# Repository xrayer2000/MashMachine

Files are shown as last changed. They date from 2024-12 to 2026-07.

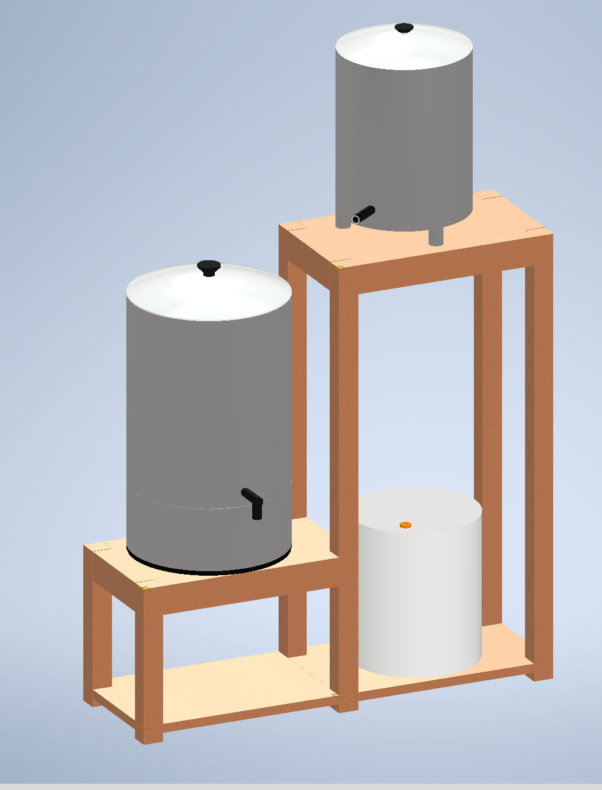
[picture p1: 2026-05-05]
InventorCad/BeerMakingShelf/5.png

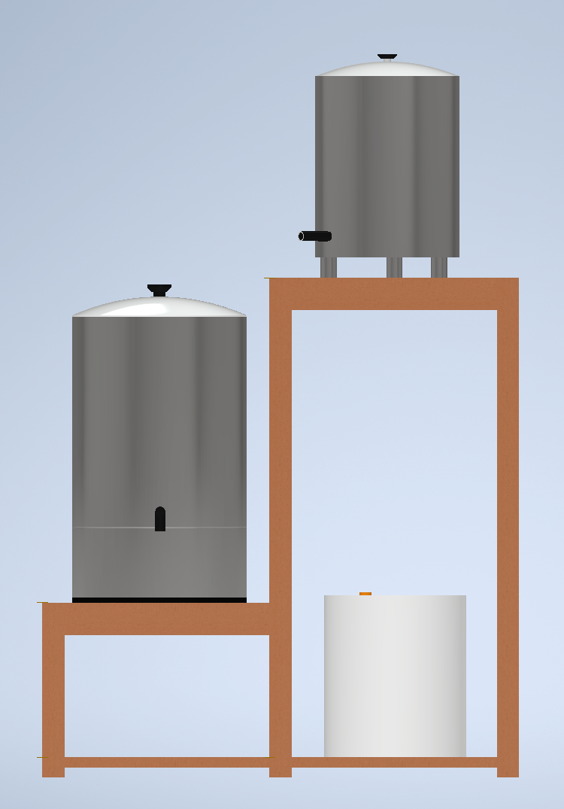
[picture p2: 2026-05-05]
InventorCad/BeerMakingShelf/6.png

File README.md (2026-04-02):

## Introduction - MashMachine
This project of mine has been a great journey for me to learn even more about my courses in the MPSYS (System Control and Mechatronics) program at Chalmers.

I have specifically used two courses in practice: SSY230 (System Identification) and SSY285 (Design of Linear Control Systems).

In the System Identification course, I used my mash tun to collect both estimation and validation data.

I used the System Identification Toolbox in MATLAB to derive state-space models for three different operating points: 50°C, 65°C, and 70°C.

EstimationData_65_75_85C

validationData_65_75_85C

ARMAX1200

All the system matrices were computed in MATLAB, and then implemented directly on the ESP32. The computational work was therefore performed offline, rather than on the microcontroller.

Once the state-space model was obtained, I used my other course, Design of Linear Control Systems, to design a controller based on this model.

I first implemented a state-feedback LQR controller, and later extended it to an LQG controller by adding a Kalman filter for state estimation.

This requires a state-space model, since LQG relies on an explicit representation of the system dynamics. In contrast to PID control, which operates only on the control error, LQG uses the model to estimate internal states and compute the control input.

With that said, the LQG controller was somewhat excessive for this application, since the system exhibits slow and stable dynamics. A PID controller would likely have been sufficient.

## Home Assistant Integration

The system is integrated with Home Assistant for monitoring and interaction.

A local Linux machine is used as a small server, running Home Assistant in a Docker container. The same setup also runs supporting services such as InfluxDB and Grafana.

Communication between the ESP32 and Home Assistant is handled using MQTT.

This setup allows:

Real-time monitoring of temperature, control signals, and system states  
Logging of data to InfluxDB for further analysis  
Visualization of system behaviour in Grafana  
Remote interaction through the Home Assistant interface  

The purpose of this integration is not only convenience, but also to enable data collection for system identification and validation, as well as to observe the controller performance over time.

## System Implementation

The starting point for this project was a very limited mash tun from Vevor, which only supported basic heating with its original controller.

The original system lacked proper control and exhibited temperature overshoot of around 2°C. To address this, the original controller was removed and replaced with a custom-built control system.

Several hardware modifications were made:

A circulation system was added using a pump  
Piping was installed to allow continuous wort circulation  
The original control electronics were replaced with an ESP32-based system  

The purpose of the circulation system is to improve temperature uniformity and make the system more suitable for control.

With the new controller, temperature regulation is significantly improved, with essentially no observable overshoot under normal operation.

In addition to the control system, several higher-level features were implemented:

-Hop timers 

-Mash programs 

-Automated process control logic 

-Home Assistant integration 

The Home Assistant integrationis is mainly for convenience, allowing me to monitor the mash process from anywhere.
The result is a system that not only performs better in terms of control, but also provides functionality expected from a more advanced brewing setup.

## Measurement System

The system initially used an NTC thermistor. This approach was abandoned due to calibration difficulty and unreliable results.

### NTC

The NTC sensor is strongly nonlinear and requires at least three reliable calibration points consisting of temperature and resistance.

In practice, this introduced several problems:

The calibration process was sensitive to noise  
Small resistance errors resulted in large temperature errors  
It was difficult to obtain consistent and accurate reference points  

This led to significant deviations between measured and actual temperature.

---

### PT100

The sensor was replaced with a PT100.

The main reasons were:

Near linear behaviour  
Simpler calibration, essentially gain and offset  
More stable and predictable measurements  

This change significantly improved both identification and state estimation.

---

## System Characteristics

The system exhibits slow dynamics and significant thermal inertia.

Measurements are affected by noise.

As a result, aggressive control is not appropriate. Stability and consistency are more important than fast response.

---

## Notes

The main difficulty in this project was not the controller design itself.

The critical parts were:

Obtaining reliable measurement data  
Constructing a model that reflects the real system  
Handling non-ideal behaviour in practice  

---

## Academic Context

This work is based on concepts from

System Identification  
Linear Control Design  

The objective has been to apply these methods to a real system rather than limiting the work to simulation.

---

## Result

A state-space model identified from experimental data  
An implemented LQG controller  
Stable temperature control on a physical system

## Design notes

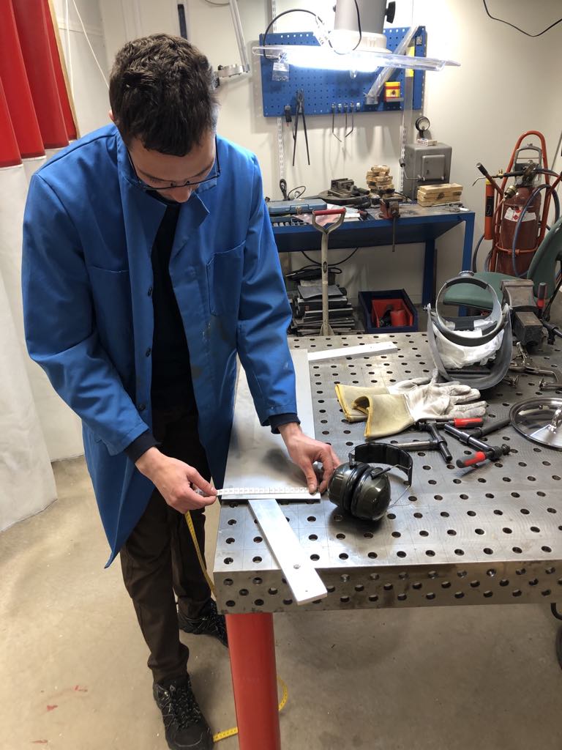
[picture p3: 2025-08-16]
PicturesAndMovies/Messenger_creation_4173f95c-cf8a-44c2-b453-e0ffb5a68564.jpeg

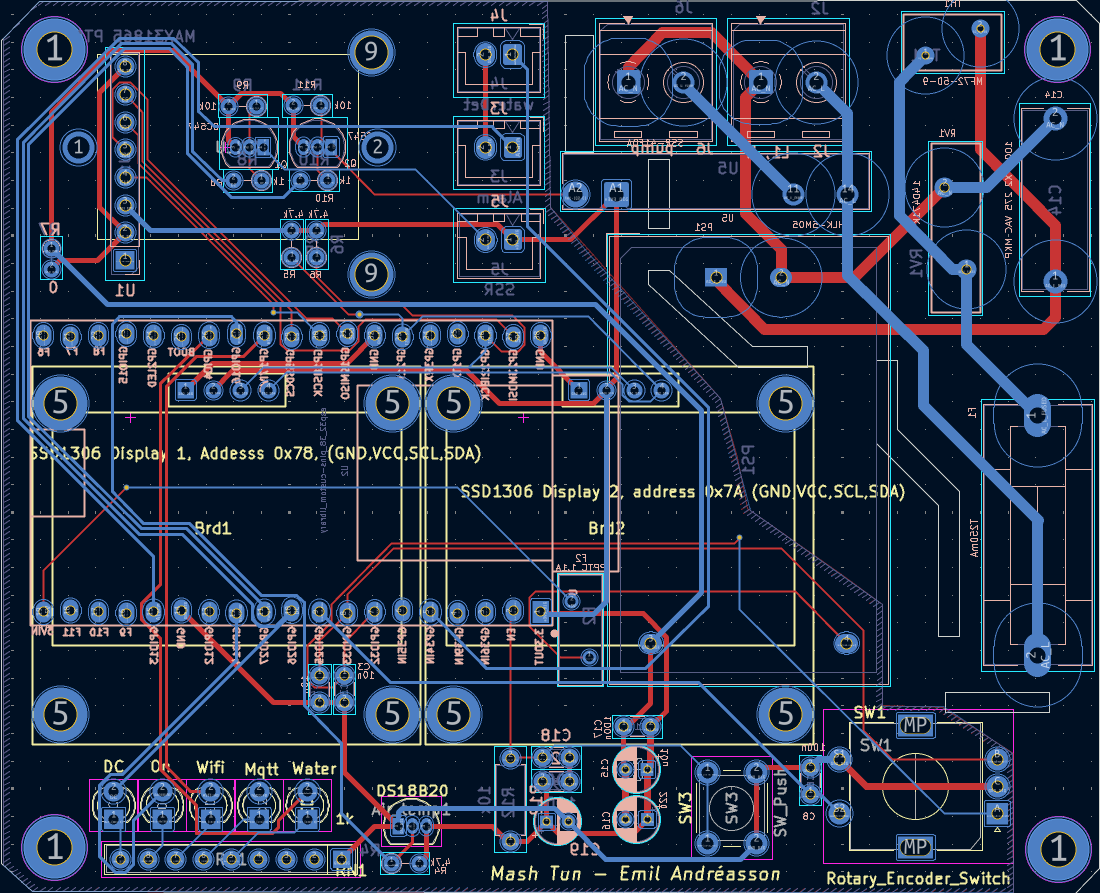
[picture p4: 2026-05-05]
InventorCad/Mash tank box V2.0/Lauter tank box/circuit board.png

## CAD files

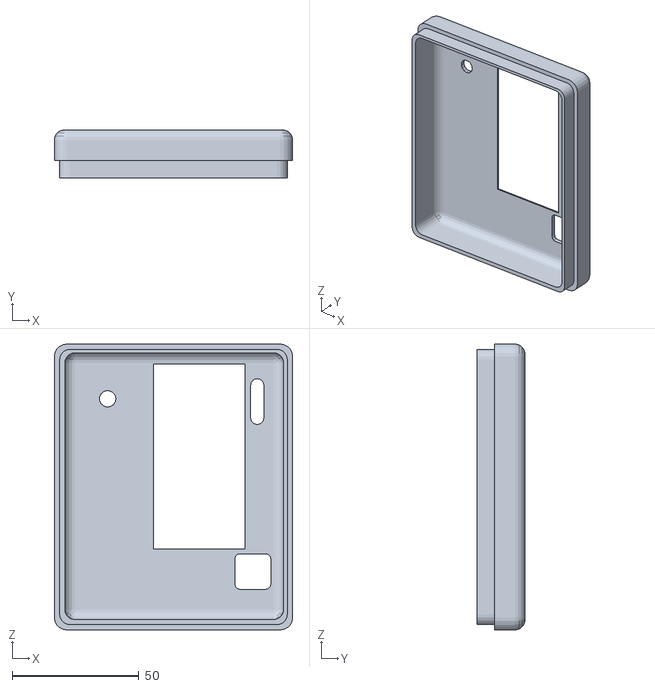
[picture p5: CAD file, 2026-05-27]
InventorCad/Lautering Tank box V2.0/lid_lautering_tank.stl
94.0 x 19.0 x 112.8

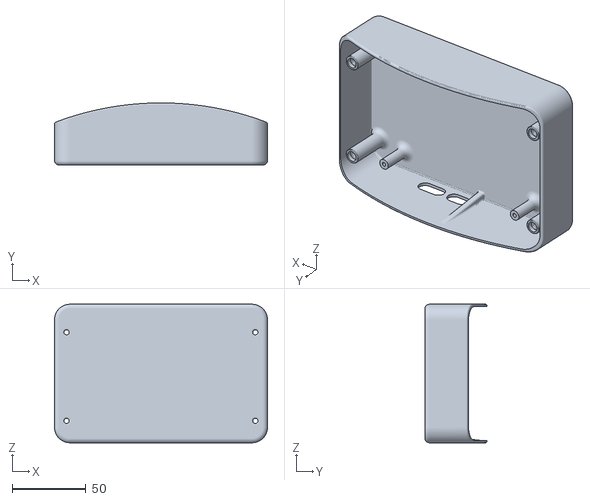
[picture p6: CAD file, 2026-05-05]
InventorCad/Mash tank box V2.0/Mash tank box/box.stl
143.9 x 42.0 x 93.7

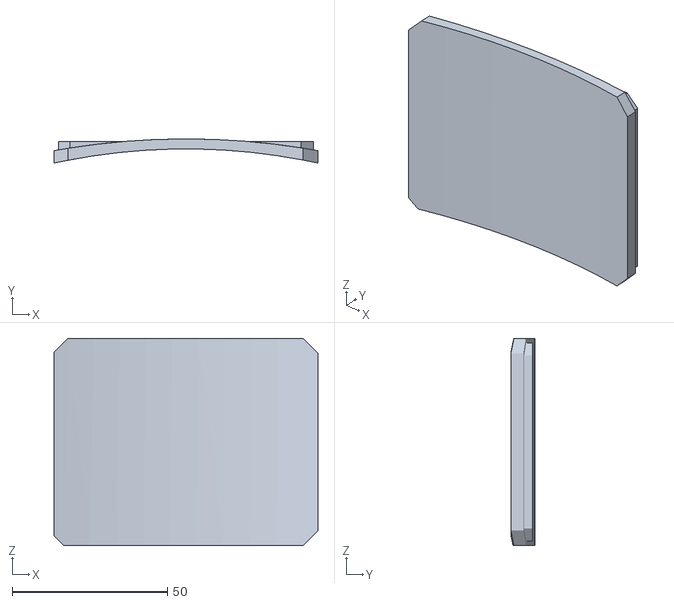
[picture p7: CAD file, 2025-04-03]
STL/Mash Tank Bottom.stl
85.1 x 7.80 x 66.8

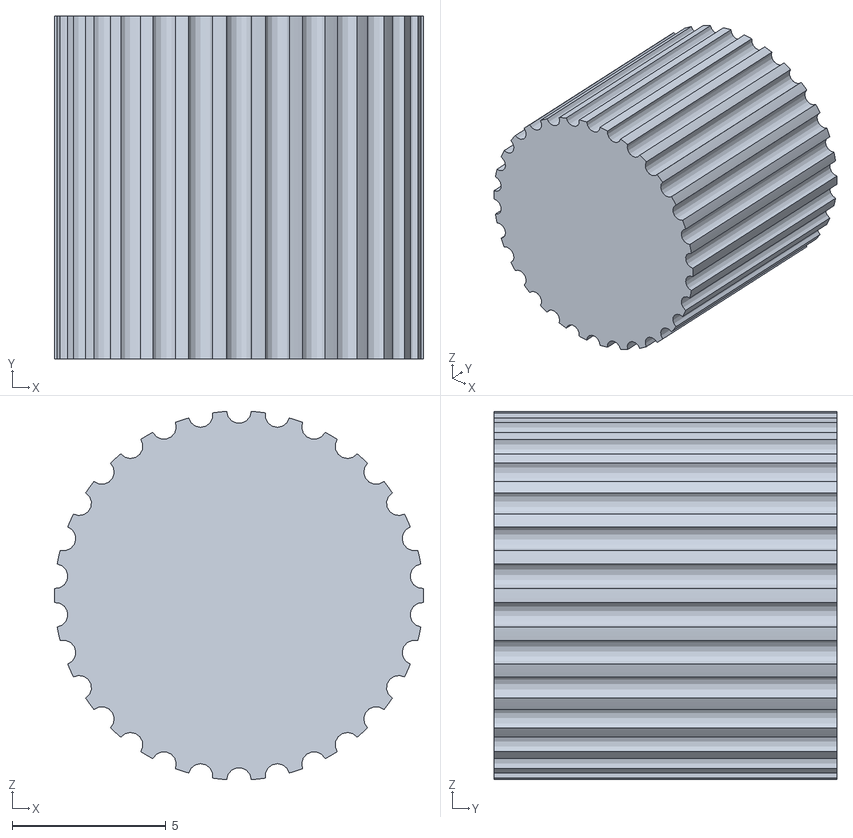
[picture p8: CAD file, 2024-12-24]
STL/Knob Rotory Encoder.stl
12.0 x 11.1 x 12.0

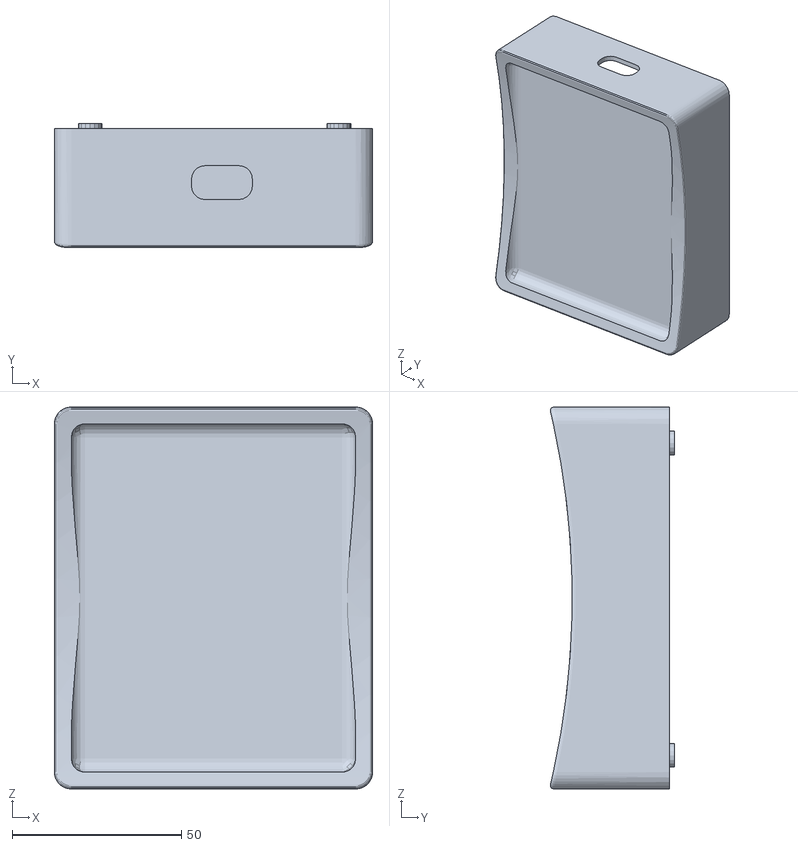
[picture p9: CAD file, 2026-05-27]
InventorCad/Lautering Tank box V2.0/lautering_tank_box.stl
94.0 x 36.7 x 112.8

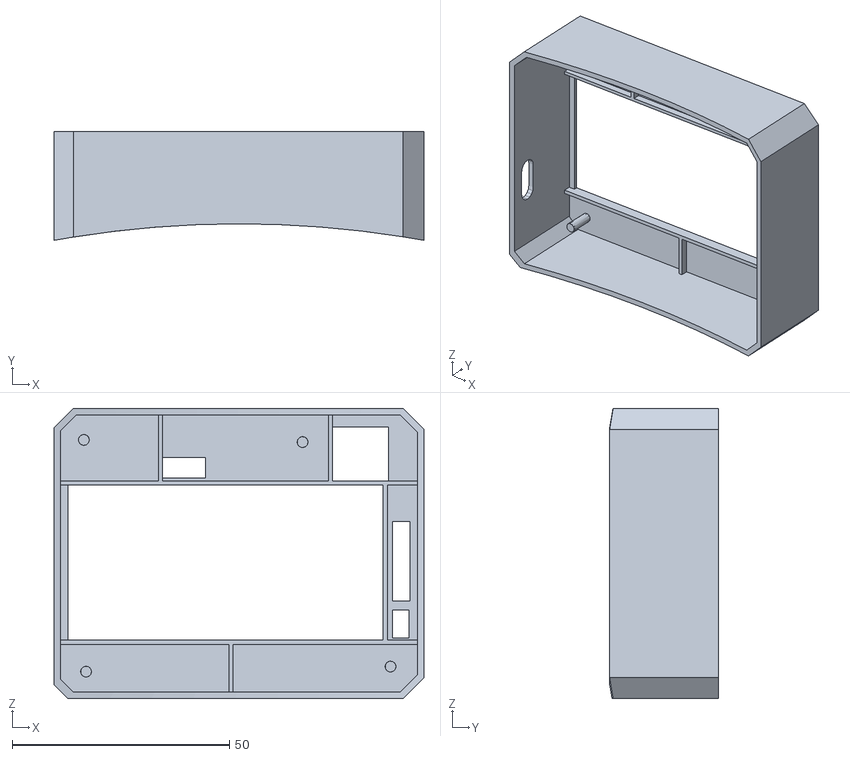
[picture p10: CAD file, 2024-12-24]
STL/Mash Tank Box.stl
85.1 x 25.0 x 66.8

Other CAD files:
InventorCad/Lautering Tank box V2.0/CE3V3SE_lid_lautering_tank.3mf
InventorCad/BeerMakingShelf/BeerMakingShelf.iam
InventorCad/BeerMakingShelf/FermentingTun.ipt
InventorCad/BeerMakingShelf/LauteringTun.ipt
InventorCad/BeerMakingShelf/MashMaschine V2.0 modell.ipt
InventorCad/BeerMakingShelf/Mäskmaskin.ipt
InventorCad/BeerMakingShelf/OldVersions/BeerMakingShelf.0038.iam
InventorCad/BeerMakingShelf/OldVersions/FermentingTun.0002.ipt
InventorCad/BeerMakingShelf/OldVersions/LauteringTun.0008.ipt
InventorCad/BeerMakingShelf/OldVersions/MashMaschine V2.0 modell.0006.ipt
InventorCad/BeerMakingShelf/OldVersions/Shelf.0003.ipt
InventorCad/BeerMakingShelf/OldVersions/selfBeamShort.0001.ipt
InventorCad/BeerMakingShelf/OldVersions/shelfBeam.0008.ipt
InventorCad/BeerMakingShelf/OldVersions/shelfBeamSide.0002.ipt
InventorCad/BeerMakingShelf/Shelf.ipt
InventorCad/BeerMakingShelf/selfBeamLong.ipt
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

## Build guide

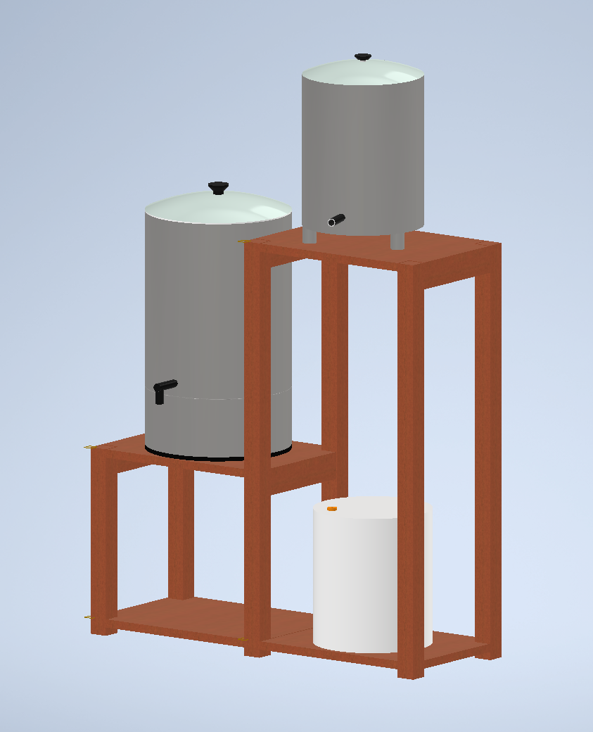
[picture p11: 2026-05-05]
InventorCad/BeerMakingShelf/3.png

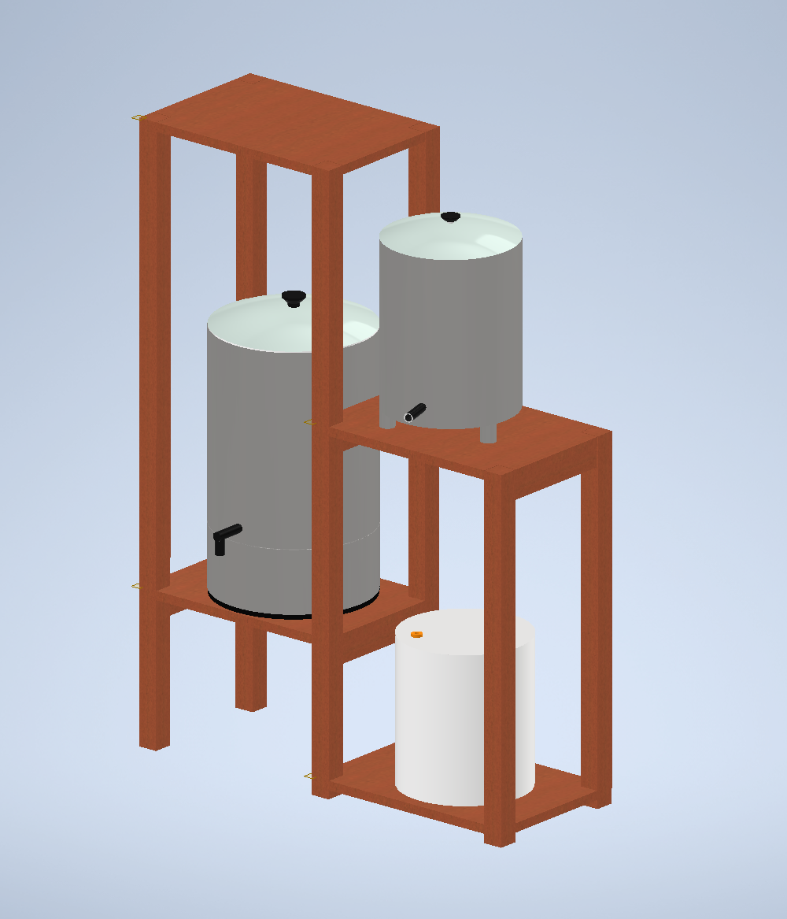
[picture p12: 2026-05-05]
InventorCad/BeerMakingShelf/2.png

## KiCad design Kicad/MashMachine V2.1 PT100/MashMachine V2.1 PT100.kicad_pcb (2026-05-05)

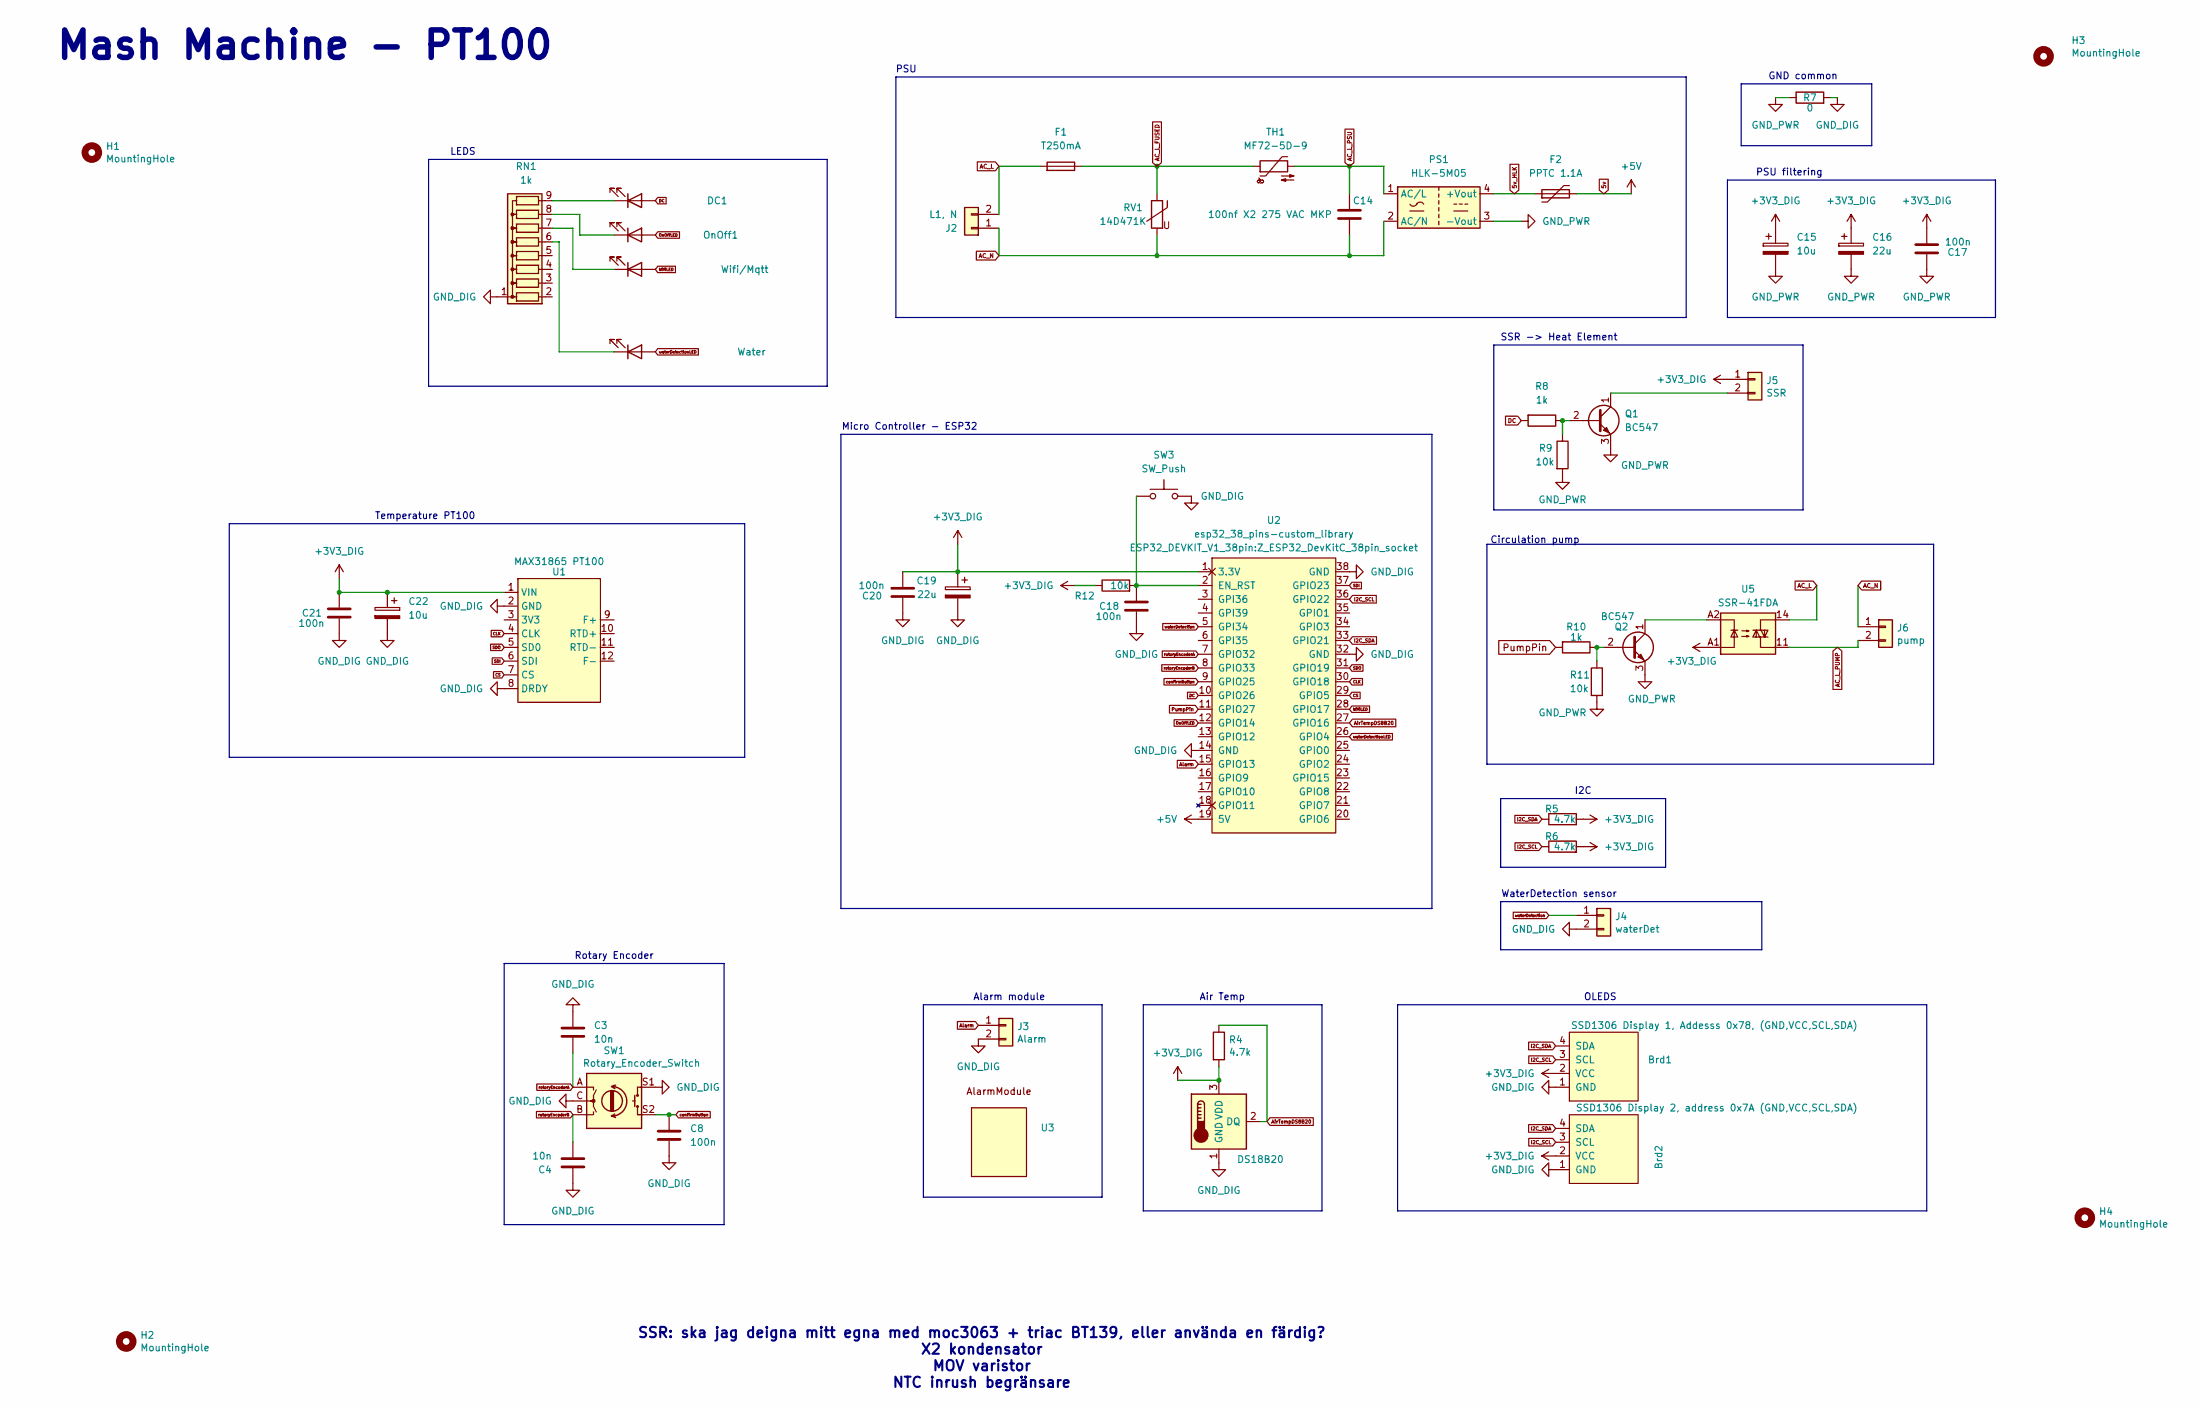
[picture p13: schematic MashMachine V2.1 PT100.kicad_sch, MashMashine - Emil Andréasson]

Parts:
Air_temp1: DS18B20; TO-92L_Inline
Brd1: SSD1306 Display 1, Addesss 0x78, (GND,VCC,SCL,SDA); ssd1306_1.3''
Brd2: SSD1306 Display 2, address 0x7A (GND,VCC,SCL,SDA); ssd1306_1.3''
C3, C4: 10n; C_Disc_D3.0mm_W1.6mm_P2.50mm
C8, C17, C18, C20, C21: 100n; C_Disc_D3.0mm_W1.6mm_P2.50mm
C14: 100nf X2 275 VAC MKP; C_Rect_L16.5mm_W6.0mm_P15.00mm_MKT
C15, C22: 10u; CP_Radial_D4.0mm_P2.00mm
C16, C19: 22u; CP_Radial_D4.0mm_P2.00mm
DC1: DC; LED_D3.0mm
F1: T250mA; Fuseholder5x20_horiz_SemiClosed_Casing10x25mm
F2: PPTC 1.1A; Fuse_BelFuse_0ZRE0016FF_L9.9mm_W3.8mm
H1, H2, H3, H4: MountingHole; MountingHole_3.2mm_M3_DIN965_Pad
J2: L1, N; TerminalBlock_RND_205-00287_1x02_P5.08mm_Horizontal
J3: Alarm; JST_XH_B2B-XH-A_1x02_P2.50mm_Vertical
J4: waterDet; JST_XH_B2B-XH-A_1x02_P2.50mm_Vertical
J5: SSR; JST_XH_B2B-XH-A_1x02_P2.50mm_Vertical
J6: pump; TerminalBlock_RND_205-00287_1x02_P5.08mm_Horizontal
LED1: Wifi/Mqtt; LED_D3.0mm
LED3: Water; LED_D3.0mm
OnOff1: On; LED_D3.0mm
PS1: HLK-5M05; Converter_ACDC_Hi-Link_HLK-5Mxx
Q1, Q2: BC547; TO-92_Inline
R4, R5, R6: 4.7k; R_Axial_DIN0204_L3.6mm_D1.6mm_P2.54mm_Vertical
R7: 0; R_Axial_DIN0204_L3.6mm_D1.6mm_P1.90mm_Vertical
R8, R10: 1k; R_Axial_DIN0204_L3.6mm_D1.6mm_P2.54mm_Vertical
R9, R11: 10k; R_Axial_DIN0204_L3.6mm_D1.6mm_P2.54mm_Vertical
R12: 10k; R_Axial_DIN0207_L6.3mm_D2.5mm_P7.62mm_Horizontal
RN1: 1k; R_Array_SIP9
RV1: 14D471K; RV_Disc_D15.5mm_W4.5mm_P7.5mm
SW1: Rotary_Encoder_Switch; RotaryEncoder_Alps_EC11E-Switch_Vertical_H20mm
SW3: SW_Push; SW_PUSH_6mm
TH1: MF72-5D-9; RV_Disc_D9mm_W5.2mm_P5mm
U1: MAX31865 PT100; PinSocket_1x08_P2.54mm_Vertical
U2: esp32_38_pins-custom_library; Z_ESP32_DevKitC_38pin_socket
U3: AlarmModule
U5: SSR-41FDA; Finder_34.81

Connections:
5v: F2.2, U2.19 (5V)
5v_HLK: F2.1, PS1.4 (+Vout)
+3V3_DIG: Air_temp1.3 (VDD), Brd1.2 (VCC), Brd2.2 (VCC), C15.1, C16.1, C17.2, C19.1, C20.2, C21.2, C22.1, J5.1, R4.2, R5.2, R6.2, R12.1, U1.1 (VIN), U2.1 (3.3V), U5.A1
AC_L: F1.2, J2.2, U5.14
AC_L_FUSED: F1.1, RV1.1, TH1.1
AC_L_PSU: C14.1, PS1.1 (AC/L), TH1.2
AC_L_PUMP: J6.2, U5.11
AC_N: C14.2, J2.1, J6.1, PS1.2 (AC/N), RV1.2
AirTempDS8B20: Air_temp1.2 (DQ), R4.1, U2.27 (GPIO16)
Alarm: J3.1, U2.15 (GPIO13)
CLK: U1.4 (CLK), U2.30 (GPIO18)
CS: U1.7 (CS), U2.29 (GPIO5)
DC: DC1.2 (A), R8.2, U2.10 (GPIO26)
GND_DIG: Air_temp1.1 (GND), Brd1.1 (GND), Brd2.1 (GND), C3.2, C4.2, C8.2, C18.1, C19.2, C20.1, C21.1, C22.2, J3.2, J4.2, R7.2, RN1.1 (common), SW1.C, SW1.S1, SW3.2, U1.2 (GND), U1.8 (DRDY), U2.14 (GND), U2.32 (GND), U2.38 (GND)
GND_PWR: C15.2, C16.2, C17.1, PS1.3 (-Vout), Q1.3 (E), Q2.3 (E), R7.1, R9.2, R11.2
I2C_SCL: Brd1.3 (SCL), Brd2.3 (SCL), R6.1, U2.36 (GPIO22)
I2C_SDA: Brd1.4 (SDA), Brd2.4 (SDA), R5.1, U2.33 (GPIO21)
unnamed: DC1.1 (K), RN1.9 (R8)
unnamed: J5.2, Q1.1 (C)
unnamed: LED1.1 (K), RN1.7 (R6)
unnamed: LED3.1 (K), RN1.6 (R5)
unnamed: OnOff1.1 (K), RN1.8 (R7)
unnamed: Q1.2 (B), R8.1, R9.1
unnamed: Q2.2 (B), R10.1, R11.1
unnamed: Q2.1 (C), U5.A2
unnamed: C18.2, R12.2, SW3.1, U2.2 (EN_RST)
OnOffLED: OnOff1.2 (A), U2.12 (GPIO14)
PumpPin: R10.2, U2.11 (GPIO27)
SDI: U1.6 (SDI), U2.37 (GPIO23)
SDO: U1.5 (SD0), U2.31 (GPIO19)
WifiLED: LED1.2 (A), U2.28 (GPIO17)
confirmButton: C8.1, SW1.S2, U2.9 (GPIO25)
rotoryEncoderA: C3.1, SW1.A, U2.7 (GPIO32)
rotoryEncoderB: C4.1, SW1.B, U2.8 (GPIO33)
waterDetection: J4.1, U2.5 (GPI34)
waterDetectionLED: LED3.2 (A), U2.26 (GPIO4)

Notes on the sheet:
LEDS
GND common
Rotary Encoder
OLEDS
Micro Controller - ESP32
Circulation pump
SSR -> Heat Element
Alarm module
Air Temp
Mash Machine - PT100
PSU filtering
SSR: ska jag deigna mitt egna med moc3063 + triac BT139, eller använda en färdig? X2 kondensator MOV varistor NTC inrush begränsare
PSU
WaterDetection sensor
I2C
Temperature PT100

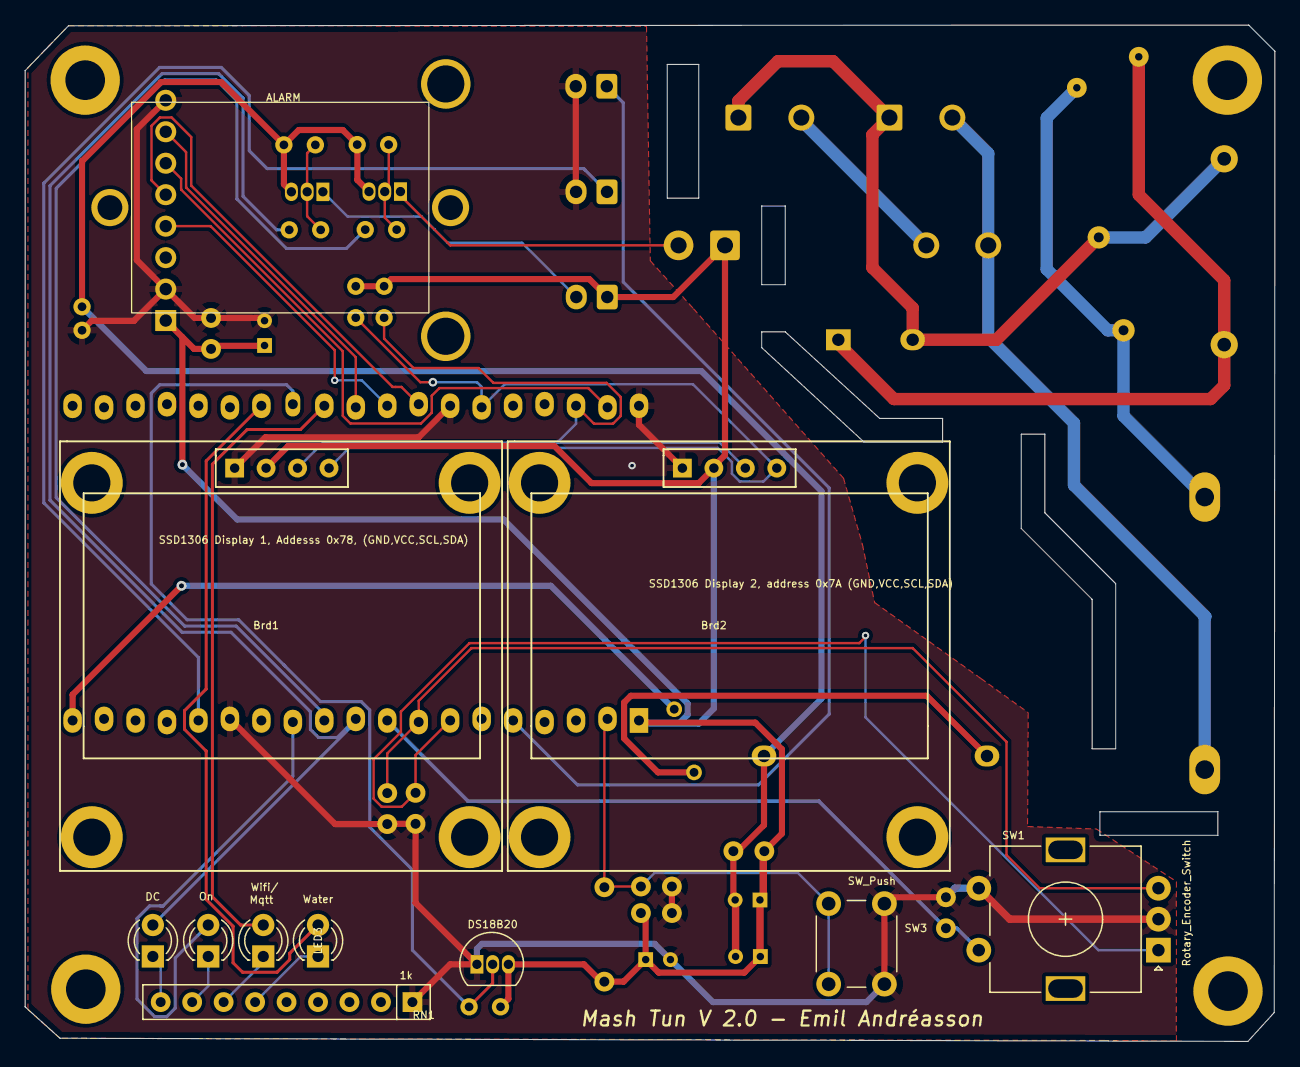
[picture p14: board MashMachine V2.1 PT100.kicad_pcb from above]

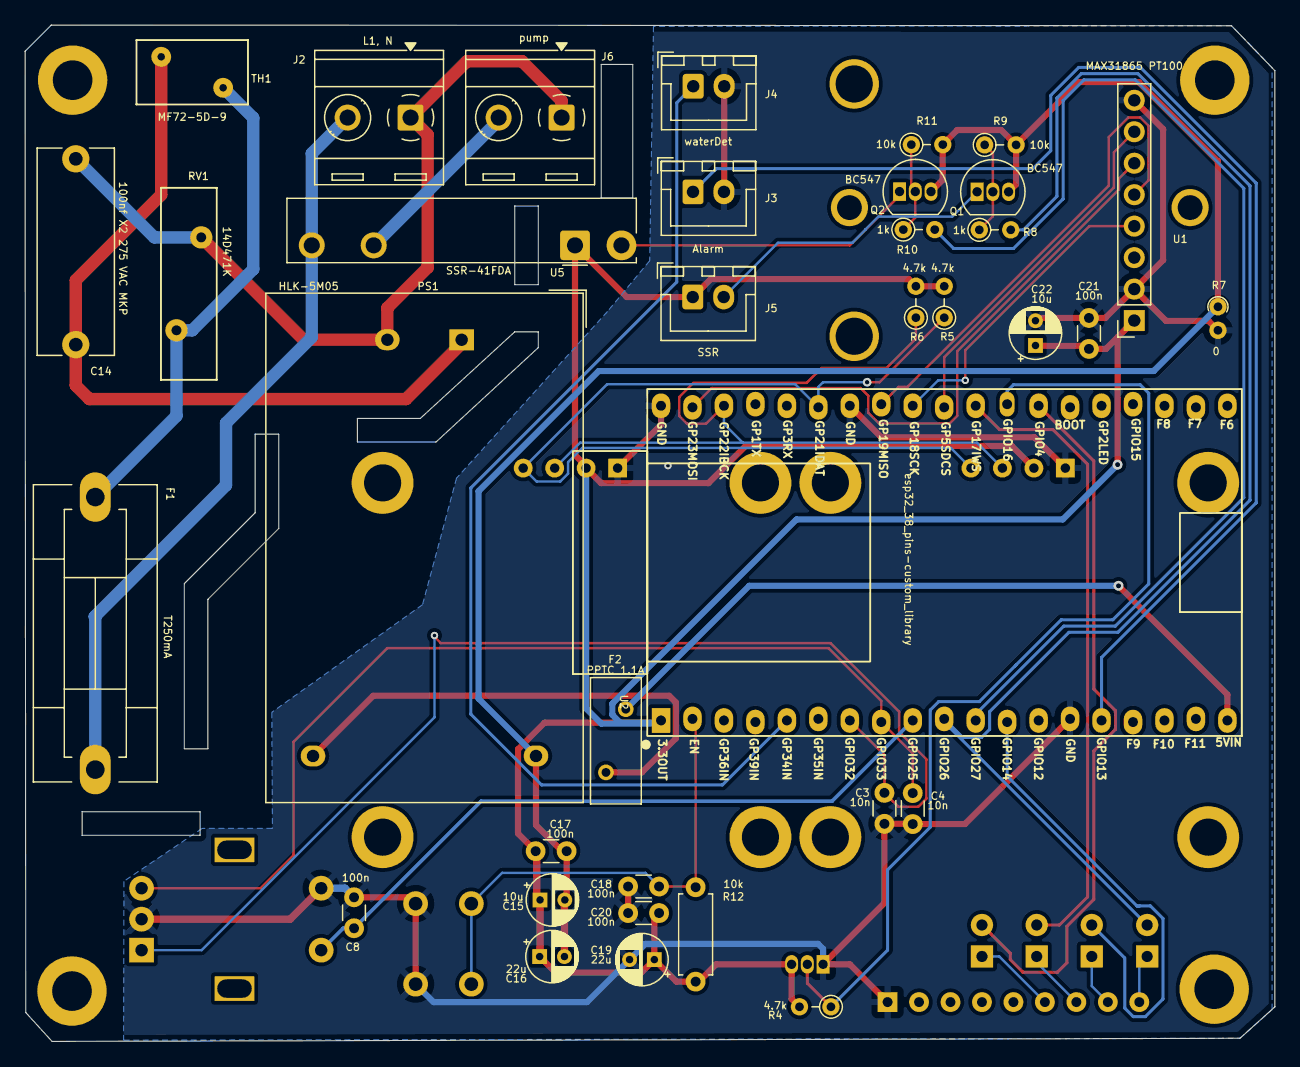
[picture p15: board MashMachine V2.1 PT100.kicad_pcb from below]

Board: 2 copper layers, 100.9 x 82.0 mm, 51 parts (36 on the bottom side), 36 nets.

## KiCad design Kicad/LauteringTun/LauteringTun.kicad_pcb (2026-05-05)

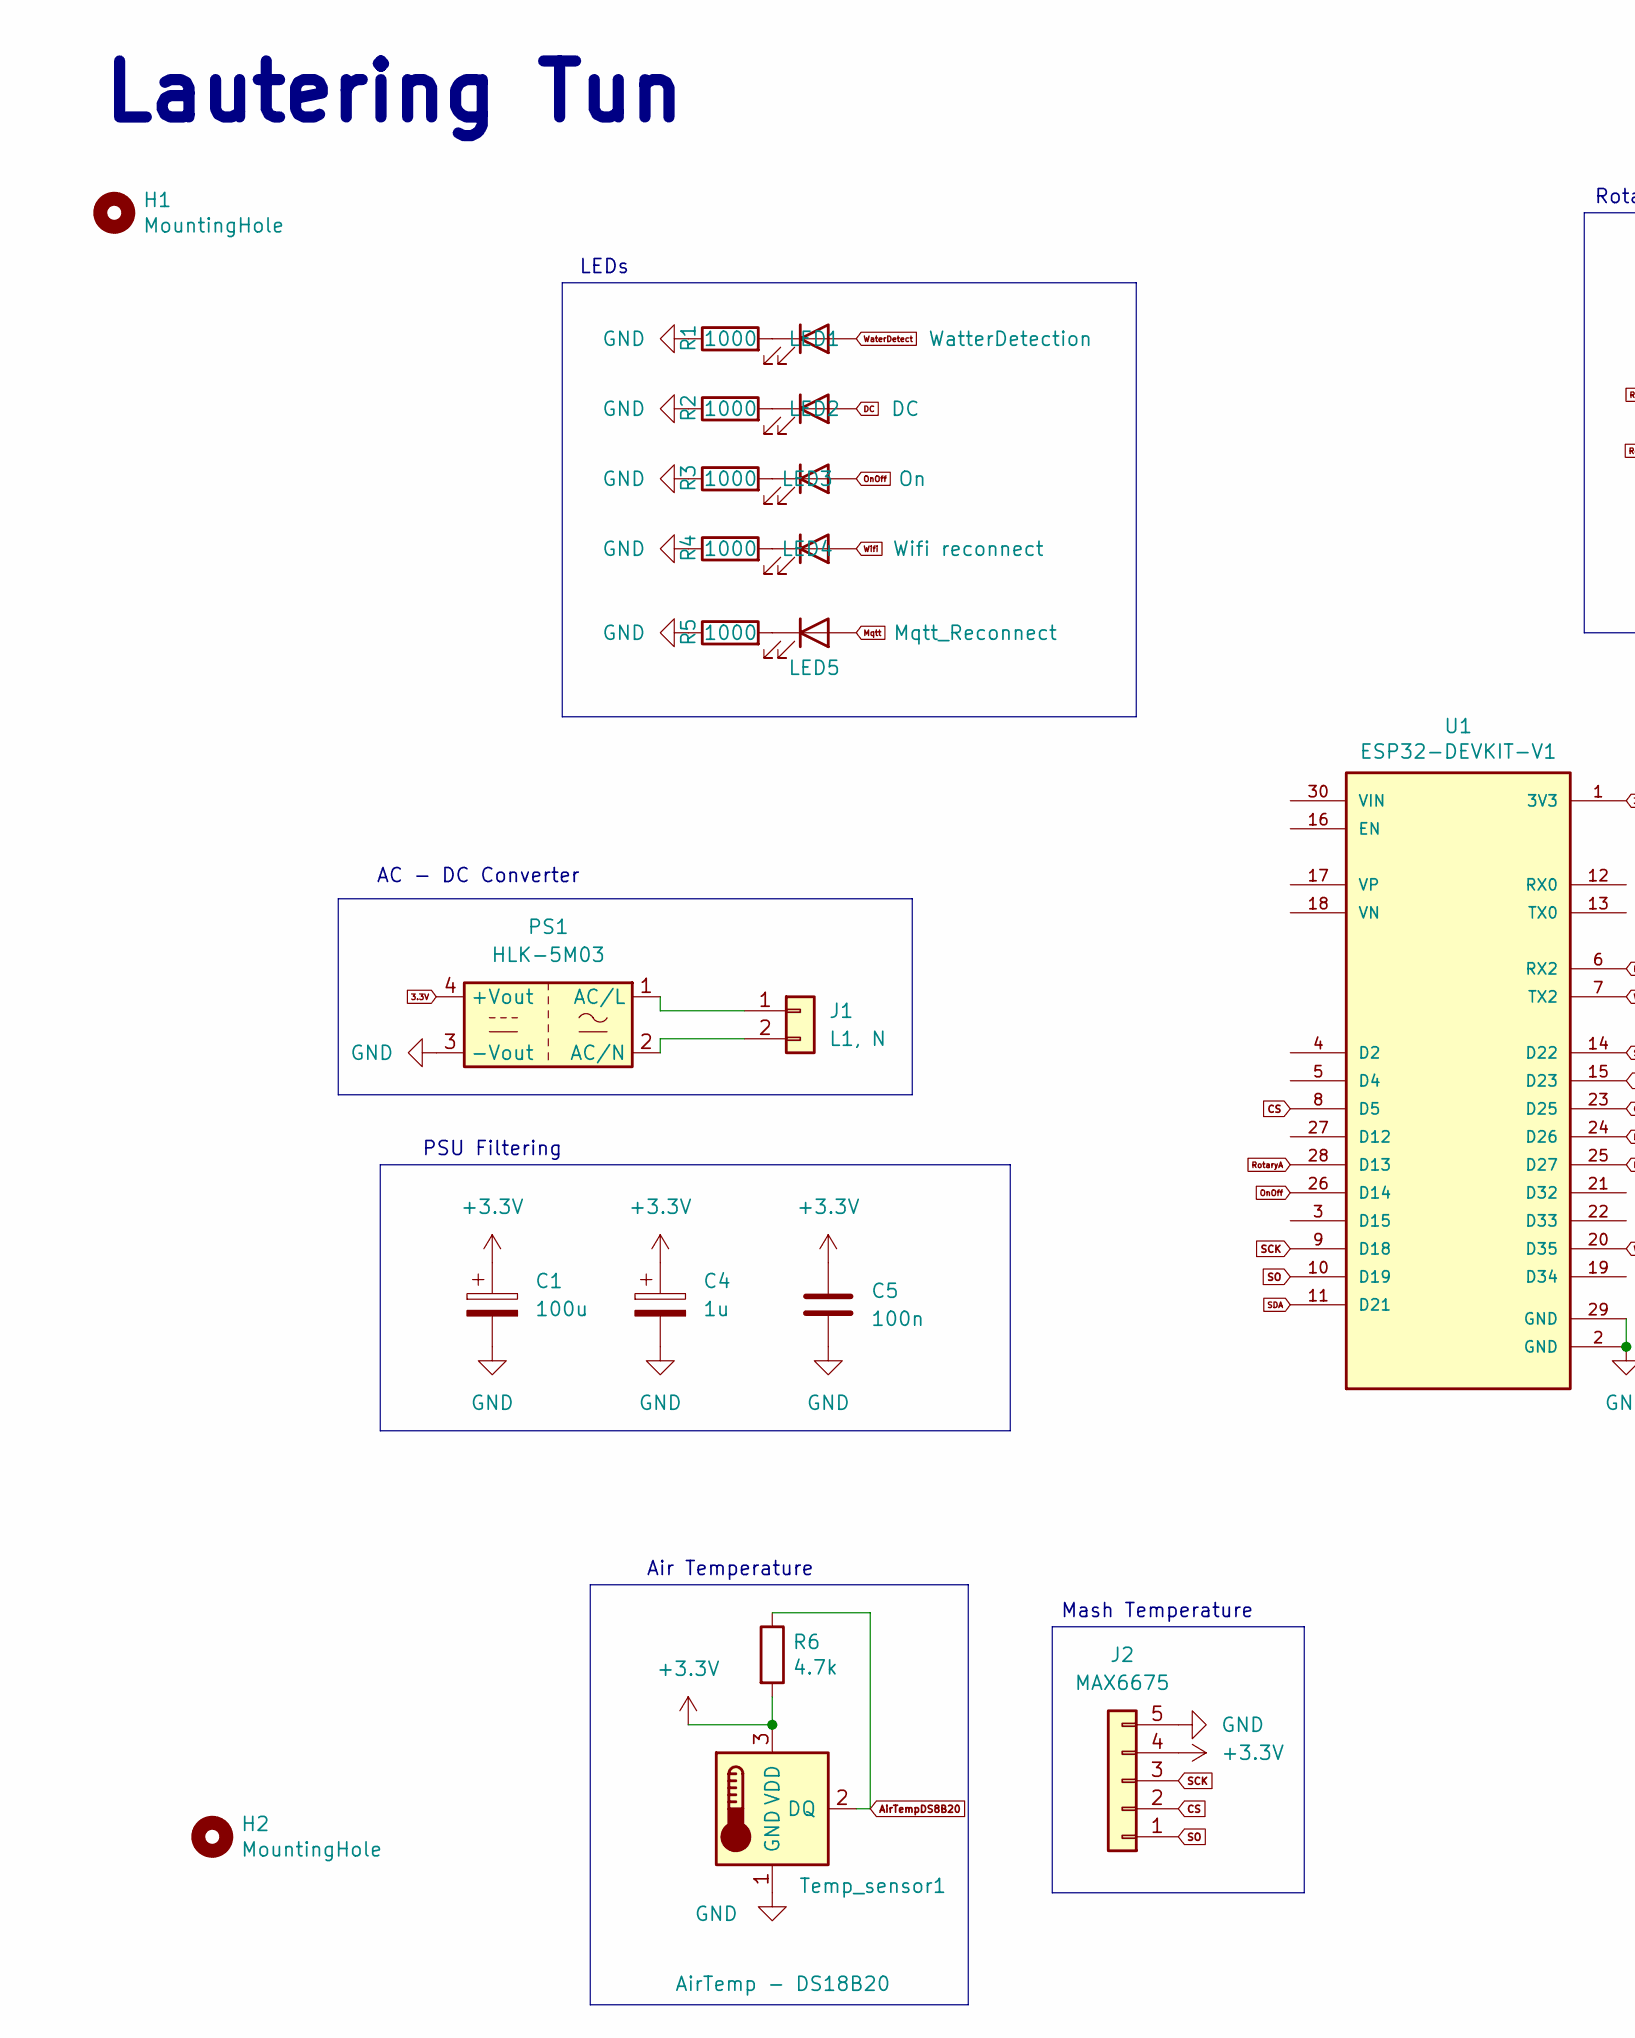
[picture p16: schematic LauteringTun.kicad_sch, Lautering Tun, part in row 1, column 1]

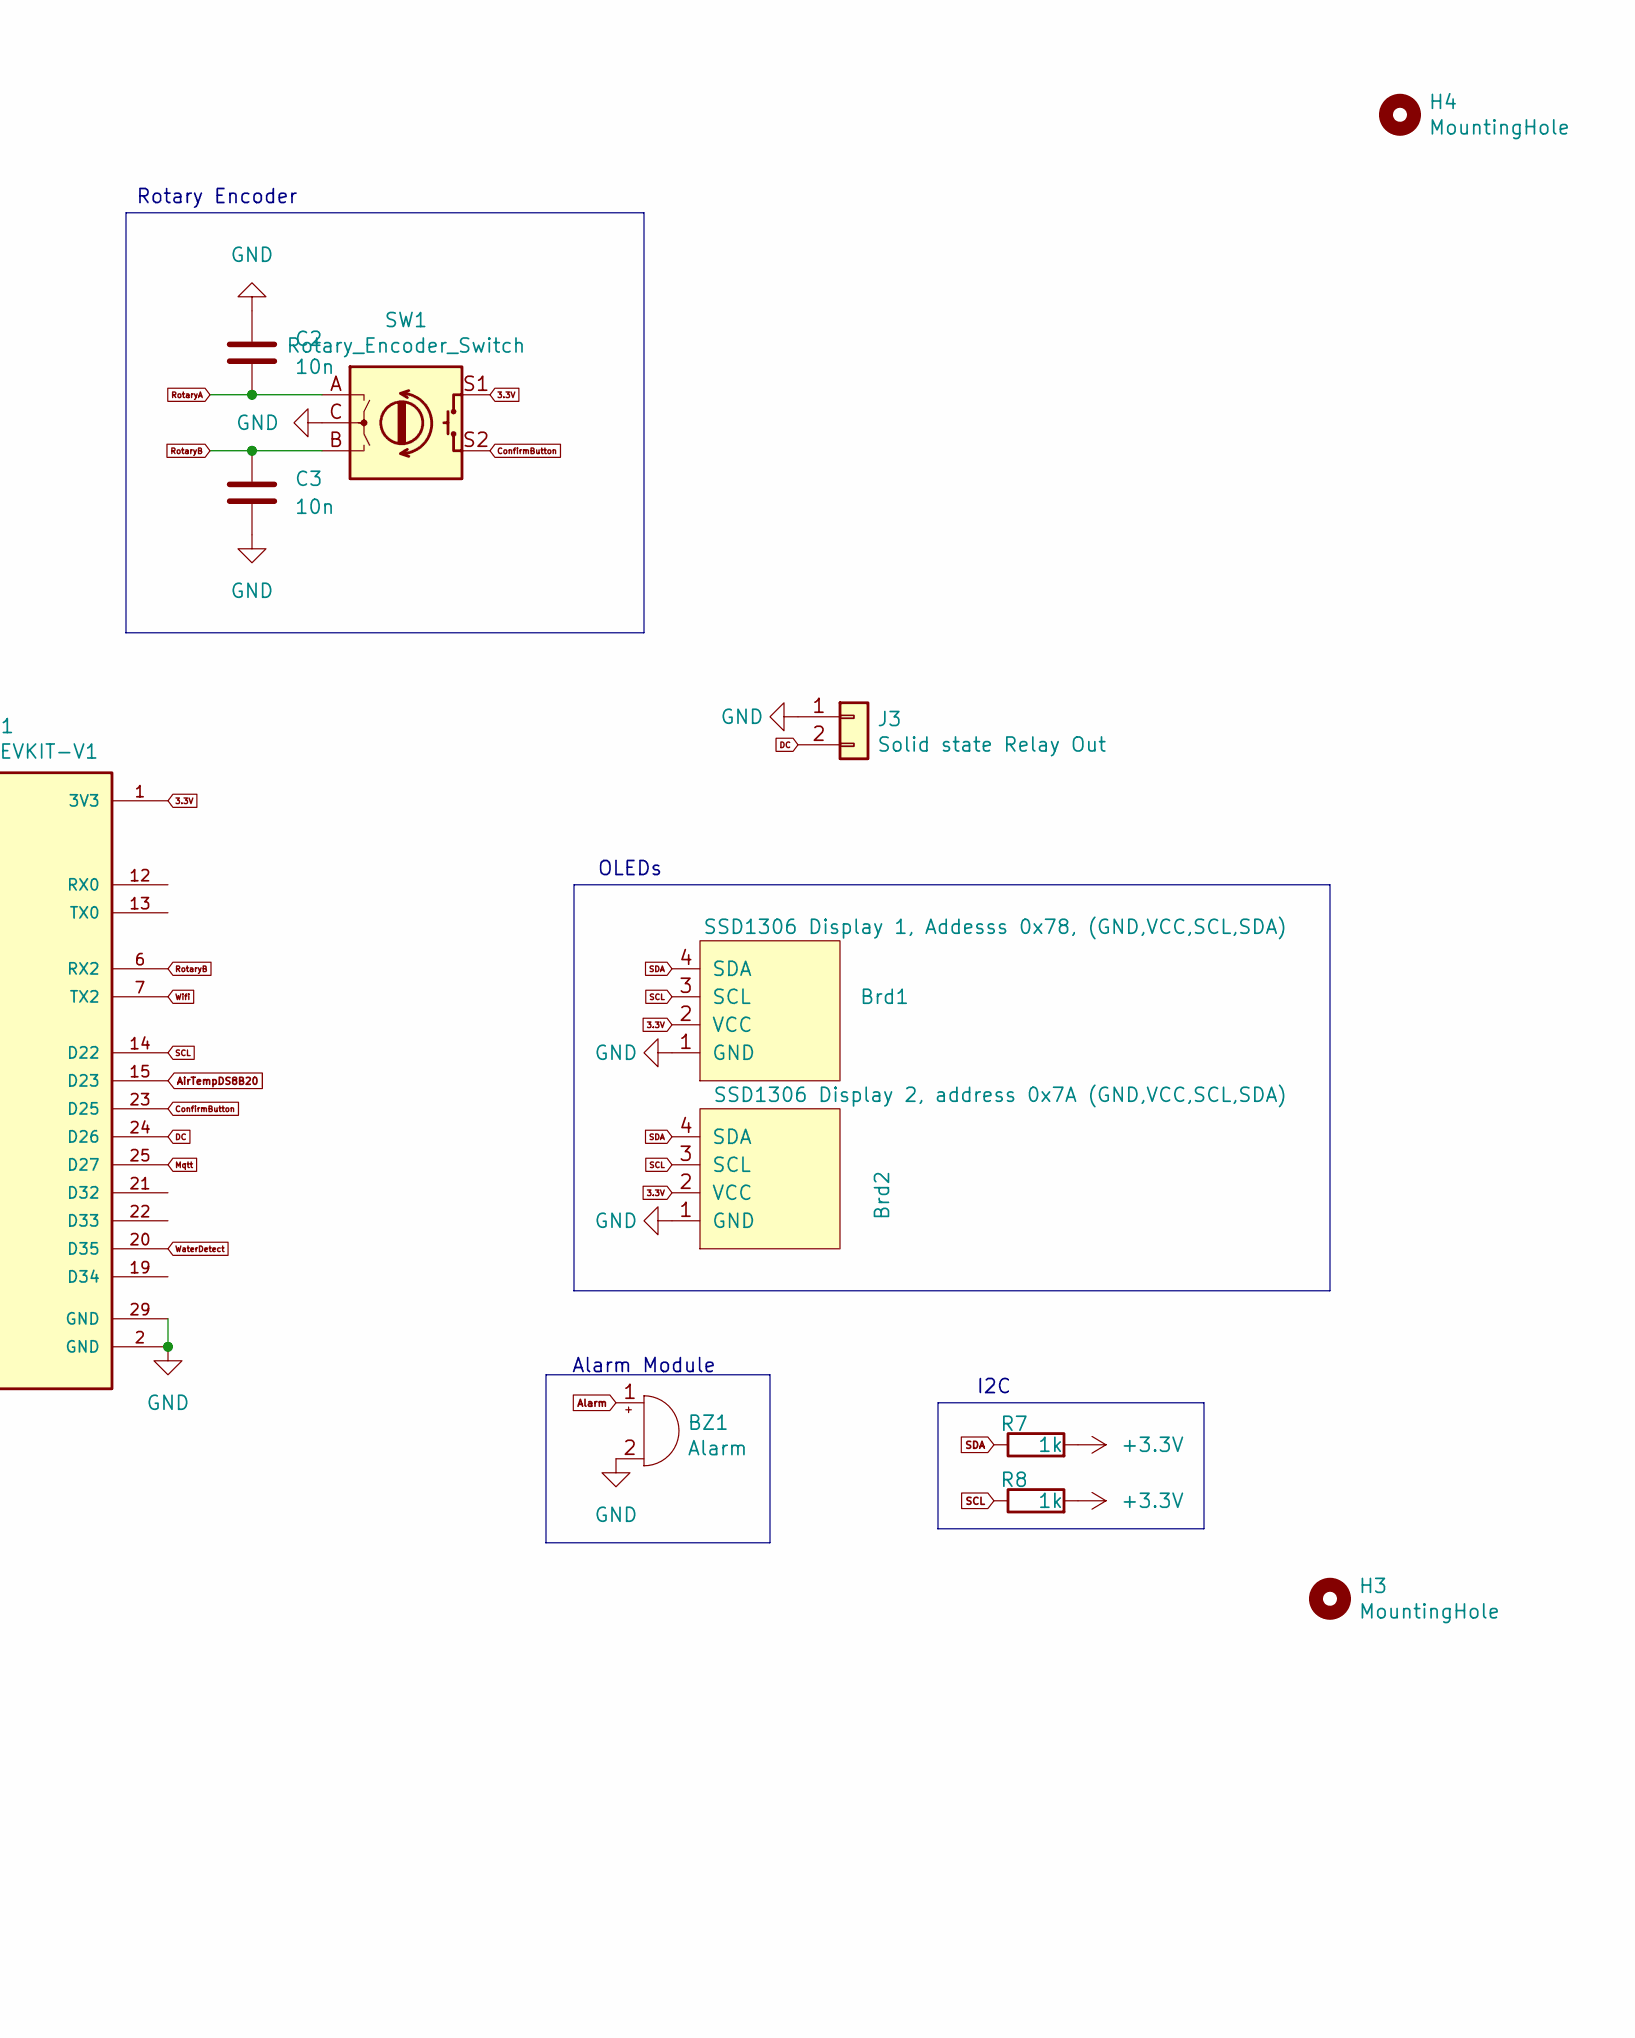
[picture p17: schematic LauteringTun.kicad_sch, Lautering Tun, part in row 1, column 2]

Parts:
BZ1: Alarm; Buzzer_12x9.5RM7.6
Brd1: SSD1306 Display 1, Addesss 0x78, (GND,VCC,SCL,SDA); ssd1306_1.3''
Brd2: SSD1306 Display 2, address 0x7A (GND,VCC,SCL,SDA); ssd1306_1.3''
C1: 100u; CP_Radial_D4.0mm_P2.00mm
C2, C3: 10n; C_Disc_D3.0mm_W1.6mm_P2.50mm
C4: 1u; CP_Radial_D4.0mm_P2.00mm
C5: 100n; C_Disc_D3.0mm_W1.6mm_P2.50mm
H1, H2, H3, H4: MountingHole; MountingHole_3.2mm_M3_DIN965_Pad
J1: L1, N; TerminalBlock_Phoenix_MKDS-1,5-2_1x02_P5.00mm_Horizontal
J2: MAX6675
J3: Solid state Relay Out; JST_XH_B2B-XH-A_1x02_P2.50mm_Vertical
LED1: WatterDetection; LED_D3.0mm
LED2: DC; LED_D3.0mm
LED3: On; LED_D3.0mm
LED4: Wifi reconnect; LED_D3.0mm
LED5: Mqtt_Reconnect; LED_D3.0mm
PS1: HLK-5M03; Converter_ACDC_Hi-Link_HLK-5Mxx
R1, R2, R3, R4, R5: 1000; R_Axial_DIN0207_L6.3mm_D2.5mm_P7.62mm_Horizontal
R6: 4.7k; R_Axial_DIN0207_L6.3mm_D2.5mm_P10.16mm_Horizontal
R7, R8: 1k; R_Axial_DIN0207_L6.3mm_D2.5mm_P7.62mm_Horizontal
SW1: Rotary_Encoder_Switch; RotaryEncoder_Alps_EC11E-Switch_Vertical_H20mm
Temp_sensor1: AirTemp - DS18B20; TO-92L_Inline
U1: ESP32-DEVKIT-V1; ESP32_DEVKIT_V1; PARTREV N/A

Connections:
3.3V: Brd1.2 (VCC), Brd2.2 (VCC), PS1.4 (+Vout), SW1.S1, U1.1 (3V3)
+3.3V: C1.1, C4.1, C5.2, J2.4, R6.2, R7.2, R8.2, Temp_sensor1.3 (VDD)
AirTempDS8B20: R6.1, Temp_sensor1.2 (DQ), U1.15 (D23)
Alarm: BZ1.1 (-)
CS: J2.2, U1.8 (D5)
ConfirmButton: SW1.S2, U1.23 (D25)
DC: J3.2, LED2.2 (A), U1.24 (D26)
GND: BZ1.2 (+), Brd1.1 (GND), Brd2.1 (GND), C1.2, C2.2, C3.1, C4.2, C5.1, J2.5, J3.1, PS1.3 (-Vout), R1.1, R2.1, R3.1, R4.1, R5.1, SW1.C, Temp_sensor1.1 (GND), U1.2 (GND), U1.29 (GND)
Mqtt: LED5.2 (A), U1.25 (D27)
unnamed: J1.1, PS1.1 (AC/L)
unnamed: J1.2, PS1.2 (AC/N)
unnamed: LED1.1 (K), R1.2
unnamed: LED2.1 (K), R2.2
unnamed: LED3.1 (K), R3.2
unnamed: LED4.1 (K), R4.2
unnamed: LED5.1 (K), R5.2
OnOff: LED3.2 (A), U1.26 (D14)
RotaryA: C2.1, SW1.A, U1.28 (D13)
RotaryB: C3.2, SW1.B, U1.6 (RX2)
SCK: J2.3, U1.9 (D18)
SCL: Brd1.3 (SCL), Brd2.3 (SCL), R8.1, U1.14 (D22)
SDA: Brd1.4 (SDA), Brd2.4 (SDA), R7.1, U1.11 (D21)
SO: J2.1, U1.10 (D19)
WaterDetect: LED1.2 (A), U1.20 (D35)
Wifi: LED4.2 (A), U1.7 (TX2)

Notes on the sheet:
I2C
Alarm Module
AC - DC Converter
Air Temperature
Lautering Tun
OLEDs
Mash Temperature
LEDs
PSU Filtering
Rotary Encoder

Board: 2 copper layers, 32 parts (2 on the bottom side), 24 nets, no tracks yet.

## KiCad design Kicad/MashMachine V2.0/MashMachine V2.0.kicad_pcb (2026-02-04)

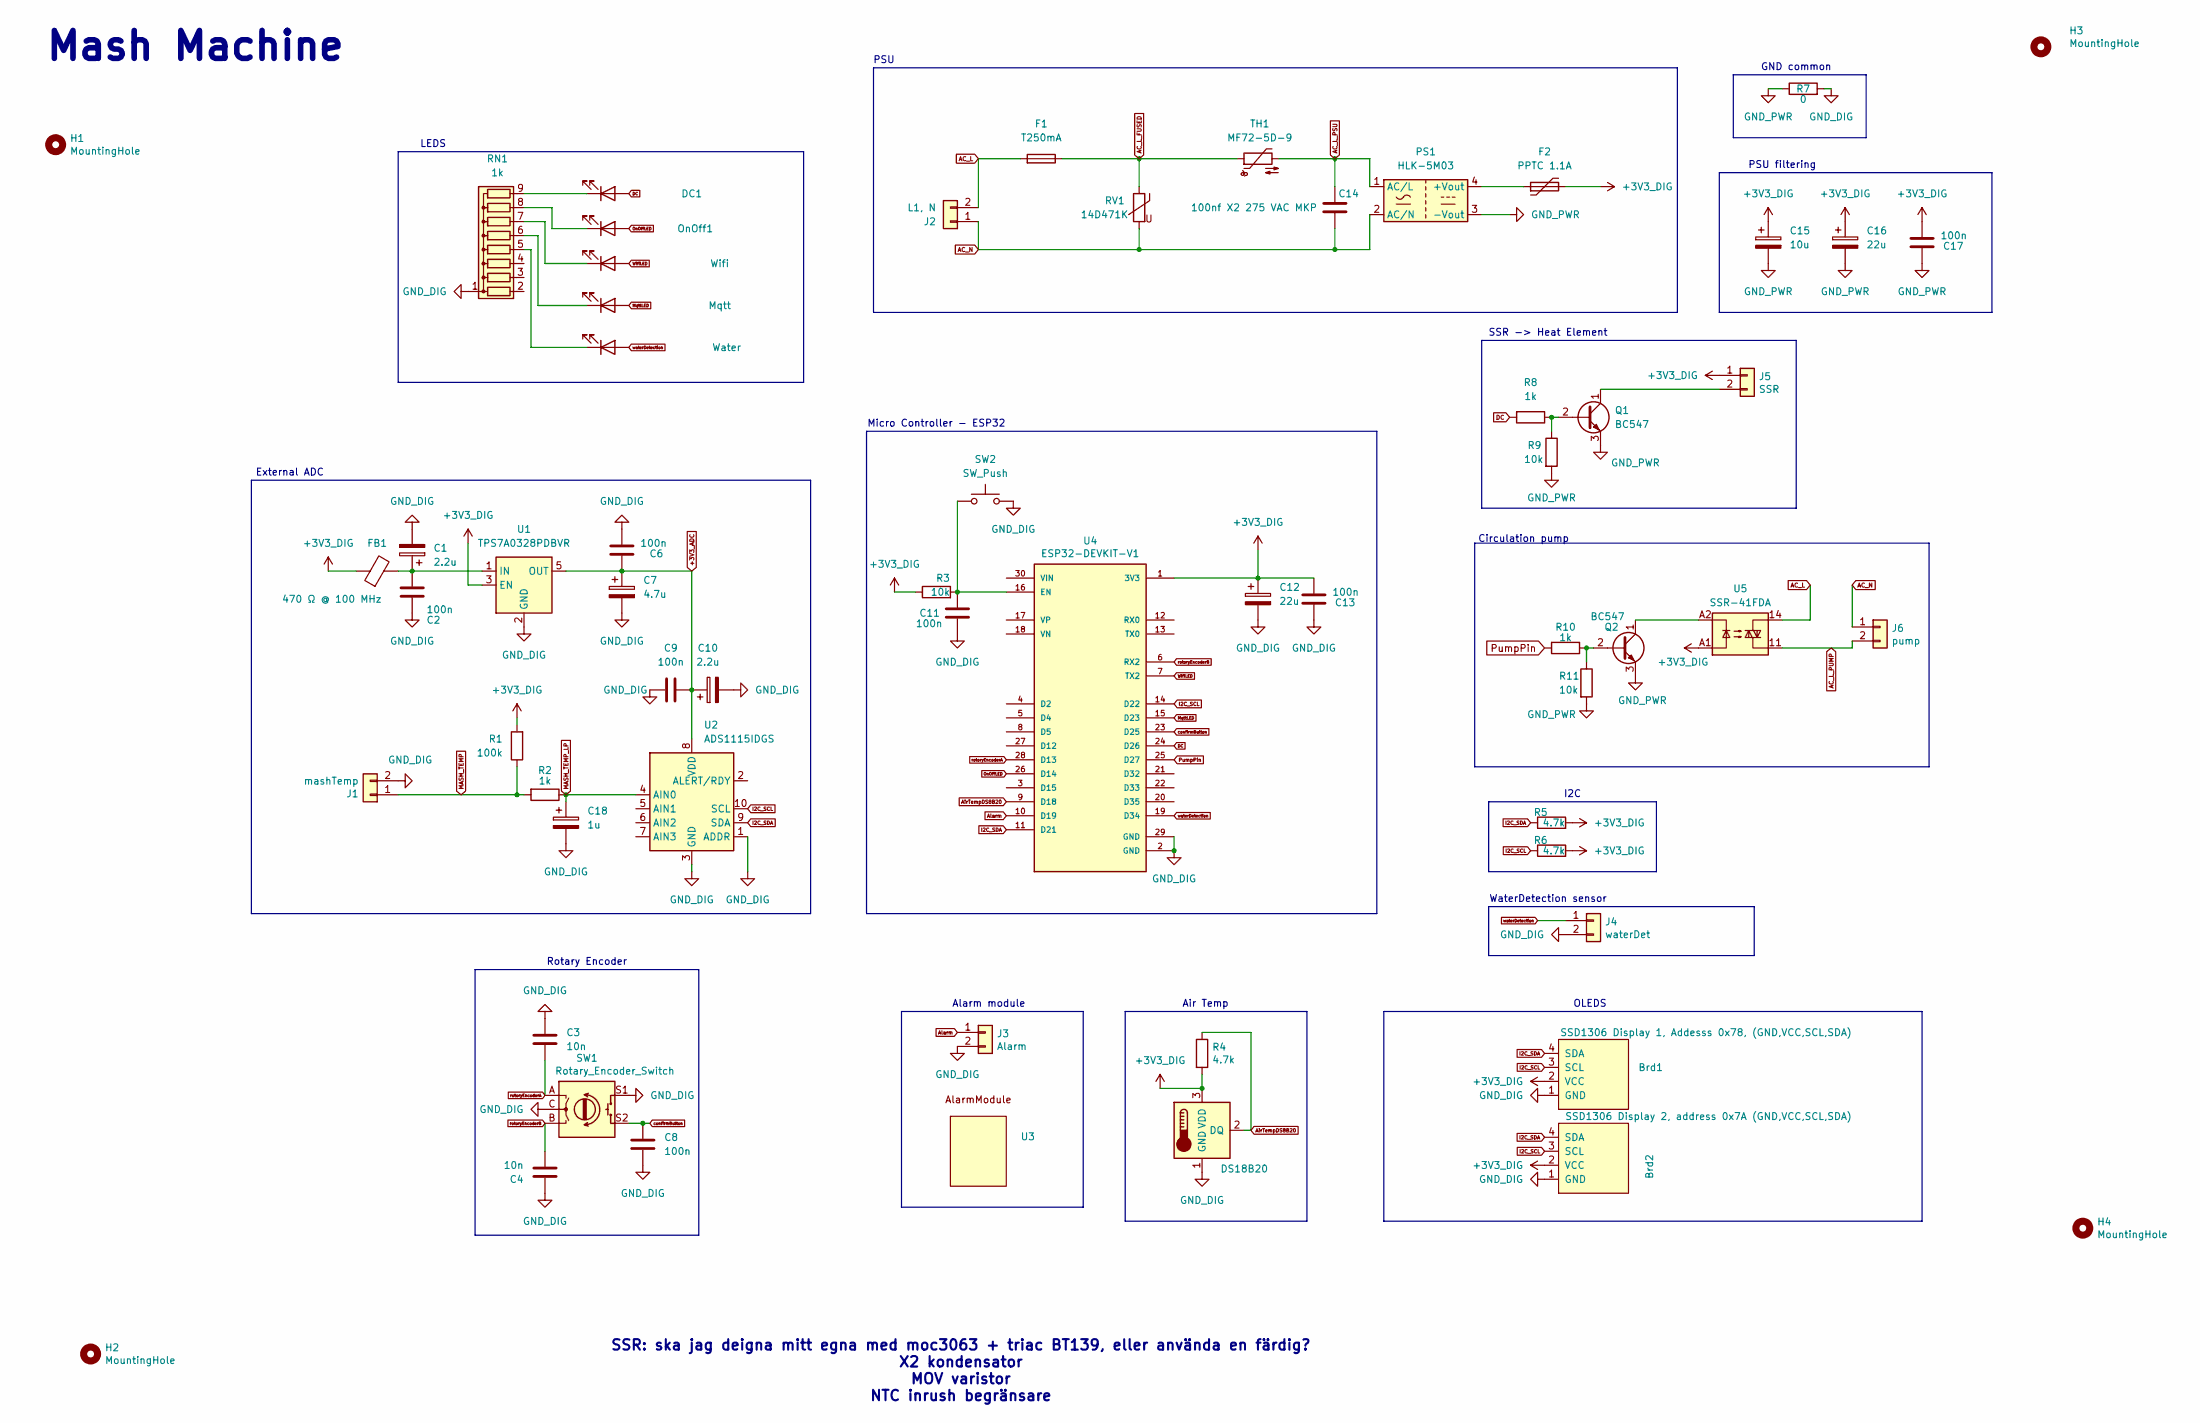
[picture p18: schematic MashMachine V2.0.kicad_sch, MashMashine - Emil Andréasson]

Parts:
Air_temp1: DS18B20; TO-92L_Inline
Brd1: SSD1306 Display 1, Addesss 0x78, (GND,VCC,SCL,SDA); ssd1306_1.3''
Brd2: SSD1306 Display 2, address 0x7A (GND,VCC,SCL,SDA); ssd1306_1.3''
C1, C10: 2.2u; CP_Radial_D4.0mm_P2.00mm
C2, C6, C8, C9, C11, C13, C17: 100n; C_Disc_D3.0mm_W1.6mm_P2.50mm
C3, C4: 10n; C_Disc_D3.0mm_W1.6mm_P2.50mm
C7: 4.7u; CP_Radial_D4.0mm_P2.00mm
C12, C16: 22u; CP_Radial_D4.0mm_P2.00mm
C14: 100nf X2 275 VAC MKP; C_Rect_L16.5mm_W6.0mm_P15.00mm_MKT
C15: 10u; CP_Radial_D4.0mm_P2.00mm
C18: 1u; CP_Radial_D4.0mm_P2.00mm
DC1: DC; LED_D3.0mm
F1: T250mA; Fuseholder5x20_horiz_SemiClosed_Casing10x25mm
F2: PPTC 1.1A; Fuse_BelFuse_0ZRE0016FF_L9.9mm_W3.8mm
FB1: 470 Ω @ 100 MHz; C_0805_2012Metric_Pad1.18x1.45mm_HandSolder
H1, H2, H3, H4: MountingHole; MountingHole_3.2mm_M3_DIN965_Pad
J1: mashTemp; JST_XH_B2B-XH-AM_1x02_P2.50mm_Vertical
J2: L1, N; TerminalBlock_RND_205-00287_1x02_P5.08mm_Horizontal
J3: Alarm; JST_XH_B2B-XH-AM_1x02_P2.50mm_Vertical
J4: waterDet; JST_XH_B2B-XH-AM_1x02_P2.50mm_Vertical
J5: SSR; JST_XH_B2B-XH-AM_1x02_P2.50mm_Vertical
J6: pump; TerminalBlock_RND_205-00287_1x02_P5.08mm_Horizontal
LED1: Wifi; LED_D3.0mm
LED2: Mqtt; LED_D3.0mm
LED3: Water; LED_D3.0mm
OnOff1: On; LED_D3.0mm
PS1: HLK-5M03; Converter_ACDC_Hi-Link_HLK-5Mxx
Q1, Q2: BC547; TO-92_Inline
R1: 100k; R_Axial_DIN0207_L6.3mm_D2.5mm_P7.62mm_Horizontal
R2: 1k; R_Axial_DIN0207_L6.3mm_D2.5mm_P7.62mm_Horizontal
R3: 10k; R_Axial_DIN0207_L6.3mm_D2.5mm_P7.62mm_Horizontal
R4, R5, R6: 4.7k; R_Axial_DIN0204_L3.6mm_D1.6mm_P2.54mm_Vertical
R7: 0; R_Axial_DIN0204_L3.6mm_D1.6mm_P1.90mm_Vertical
R8, R10: 1k; R_Axial_DIN0204_L3.6mm_D1.6mm_P2.54mm_Vertical
R9, R11: 10k; R_Axial_DIN0204_L3.6mm_D1.6mm_P2.54mm_Vertical
RN1: 1k; R_Array_SIP9
RV1: 14D471K; RV_Disc_D15.5mm_W4.5mm_P7.5mm
SW1: Rotary_Encoder_Switch; RotaryEncoder_Alps_EC11E-Switch_Vertical_H20mm
SW2: SW_Push; SW_PUSH_6mm
TH1: MF72-5D-9; RV_Disc_D9mm_W5.2mm_P5mm
U1: TPS7A0328PDBVR; SOT-23-5
U2: ADS1115IDGS; PinSocket_1x10_P2.54mm_Vertical
U3: AlarmModule
U4: ESP32-DEVKIT-V1; ESP32_DEVKIT_V1; PARTREV N/A
U5: SSR-41FDA; Finder_34.81

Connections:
+3V3_ADC: C6.1, C7.1, C9.1, C10.1, U1.5 (OUT), U2.8 (VDD)
+3V3_DIG: Air_temp1.3 (VDD), Brd1.2 (VCC), Brd2.2 (VCC), C12.1, C13.2, C15.1, C16.1, C17.2, F2.2, FB1.1, J5.1, R1.2, R3.1, R4.2, R5.2, R6.2, U1.3 (EN), U4.1 (3V3), U5.A1
AC_L: F1.2, J2.2, U5.14
AC_L_FUSED: F1.1, RV1.1, TH1.1
AC_L_PSU: C14.1, PS1.1 (AC/L), TH1.2
AC_L_PUMP: J6.2, U5.11
AC_N: C14.2, J2.1, J6.1, PS1.2 (AC/N), RV1.2
AirTempDS8B20: Air_temp1.2 (DQ), R4.1, U4.9 (D18)
Alarm: J3.1, U4.10 (D19)
DC: DC1.2 (A), R8.2, U4.24 (D26)
GND_DIG: Air_temp1.1 (GND), Brd1.1 (GND), Brd2.1 (GND), C1.2, C2.2, C3.2, C4.2, C6.2, C7.2, C8.2, C9.2, C10.2, C11.1, C12.2, C13.1, C18.2, J1.2, J3.2, J4.2, R7.2, RN1.1 (common), SW1.C, SW1.S1, SW2.2, U1.2 (GND), U2.1 (ADDR), U2.3 (GND), U4.2 (GND), U4.29 (GND)
GND_PWR: C15.2, C16.2, C17.1, PS1.3 (-Vout), Q1.3 (E), Q2.3 (E), R7.1, R9.2, R11.2
I2C_SCL: Brd1.3 (SCL), Brd2.3 (SCL), R6.1, U2.10 (SCL), U4.14 (D22)
I2C_SDA: Brd1.4 (SDA), Brd2.4 (SDA), R5.1, U2.9 (SDA), U4.11 (D21)
MASH_TEMP: J1.1, R1.1, R2.2
MASH_TEMP_LP: C18.1, R2.1, U2.4 (AIN0)
MqttLED: LED2.2 (A), U4.15 (D23)
unnamed: DC1.1 (K), RN1.9 (R8)
unnamed: J5.2, Q1.1 (C)
unnamed: LED1.1 (K), RN1.7 (R6)
unnamed: LED2.1 (K), RN1.6 (R5)
unnamed: LED3.1 (K), RN1.5 (R4)
unnamed: OnOff1.1 (K), RN1.8 (R7)
unnamed: F2.1, PS1.4 (+Vout)
unnamed: Q1.2 (B), R8.1, R9.1
unnamed: Q2.2 (B), R10.1, R11.1
unnamed: Q2.1 (C), U5.A2
unnamed: C1.1, C2.1, FB1.2, U1.1 (IN)
unnamed: C11.2, R3.2, SW2.1, U4.16 (EN)
OnOffLED: OnOff1.2 (A), U4.26 (D14)
PumpPin: R10.2, U4.25 (D27)
WifiLED: LED1.2 (A), U4.7 (TX2)
confirmButton: C8.1, SW1.S2, U4.23 (D25)
rotoryEncoderA: C3.1, SW1.A, U4.28 (D13)
rotoryEncoderB: C4.1, SW1.B, U4.6 (RX2)
waterDetection: J4.1, LED3.2 (A), U4.19 (D34)

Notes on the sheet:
External ADC
LEDS
GND common
Rotary Encoder
OLEDS
Micro Controller - ESP32
Circulation pump
SSR -> Heat Element
Alarm module
Air Temp
Mash Machine
PSU filtering
SSR: ska jag deigna mitt egna med moc3063 + triac BT139, eller använda en färdig? X2 kondensator MOV varistor NTC inrush begränsare
PSU
WaterDetection sensor
I2C

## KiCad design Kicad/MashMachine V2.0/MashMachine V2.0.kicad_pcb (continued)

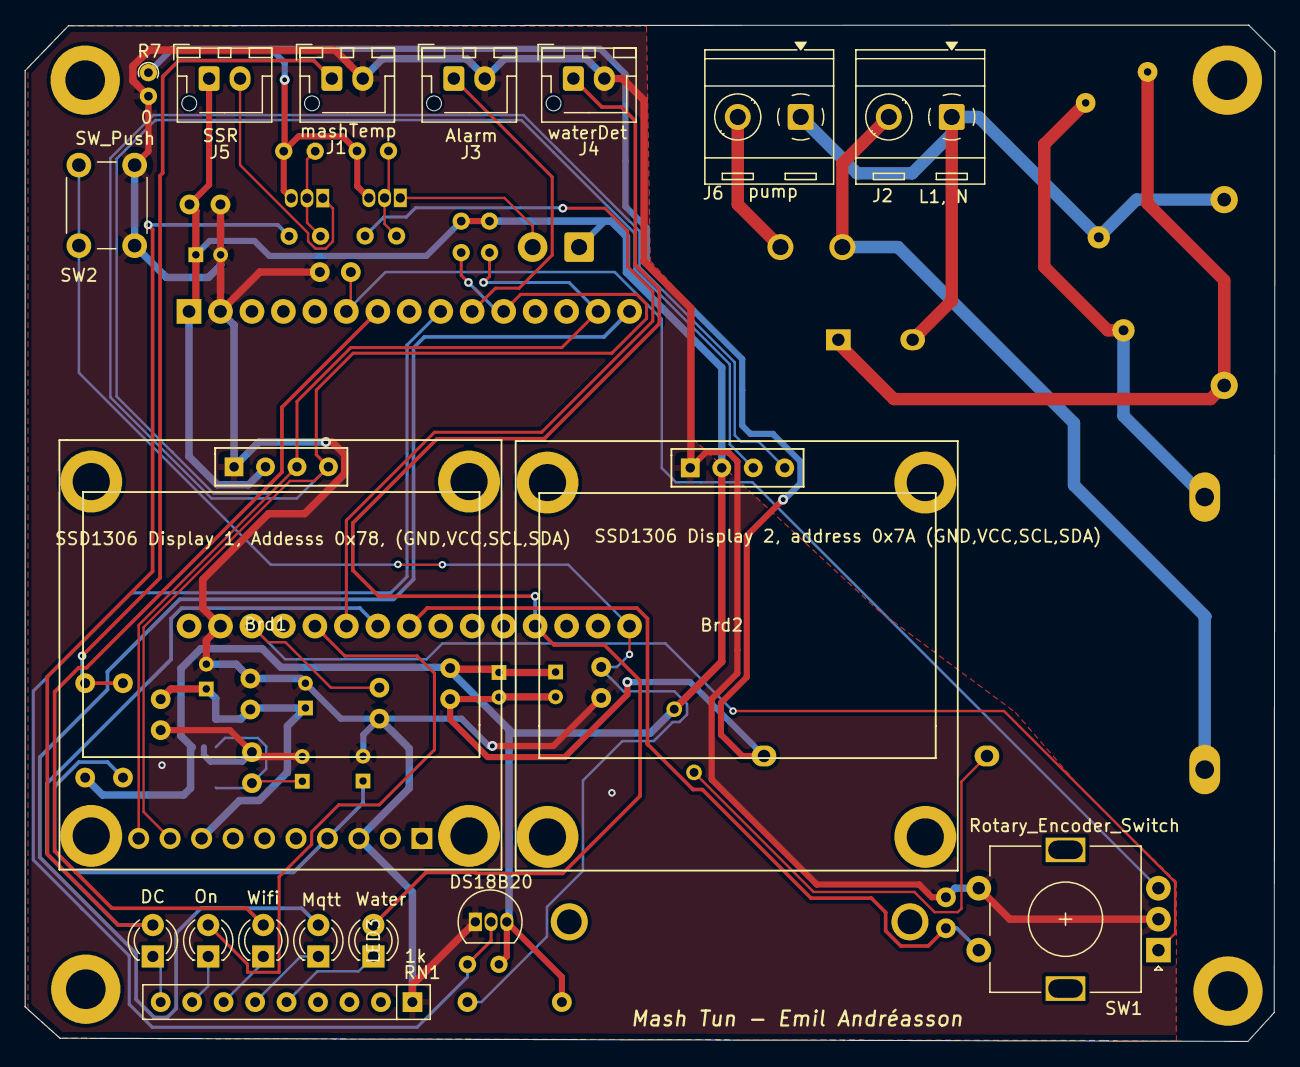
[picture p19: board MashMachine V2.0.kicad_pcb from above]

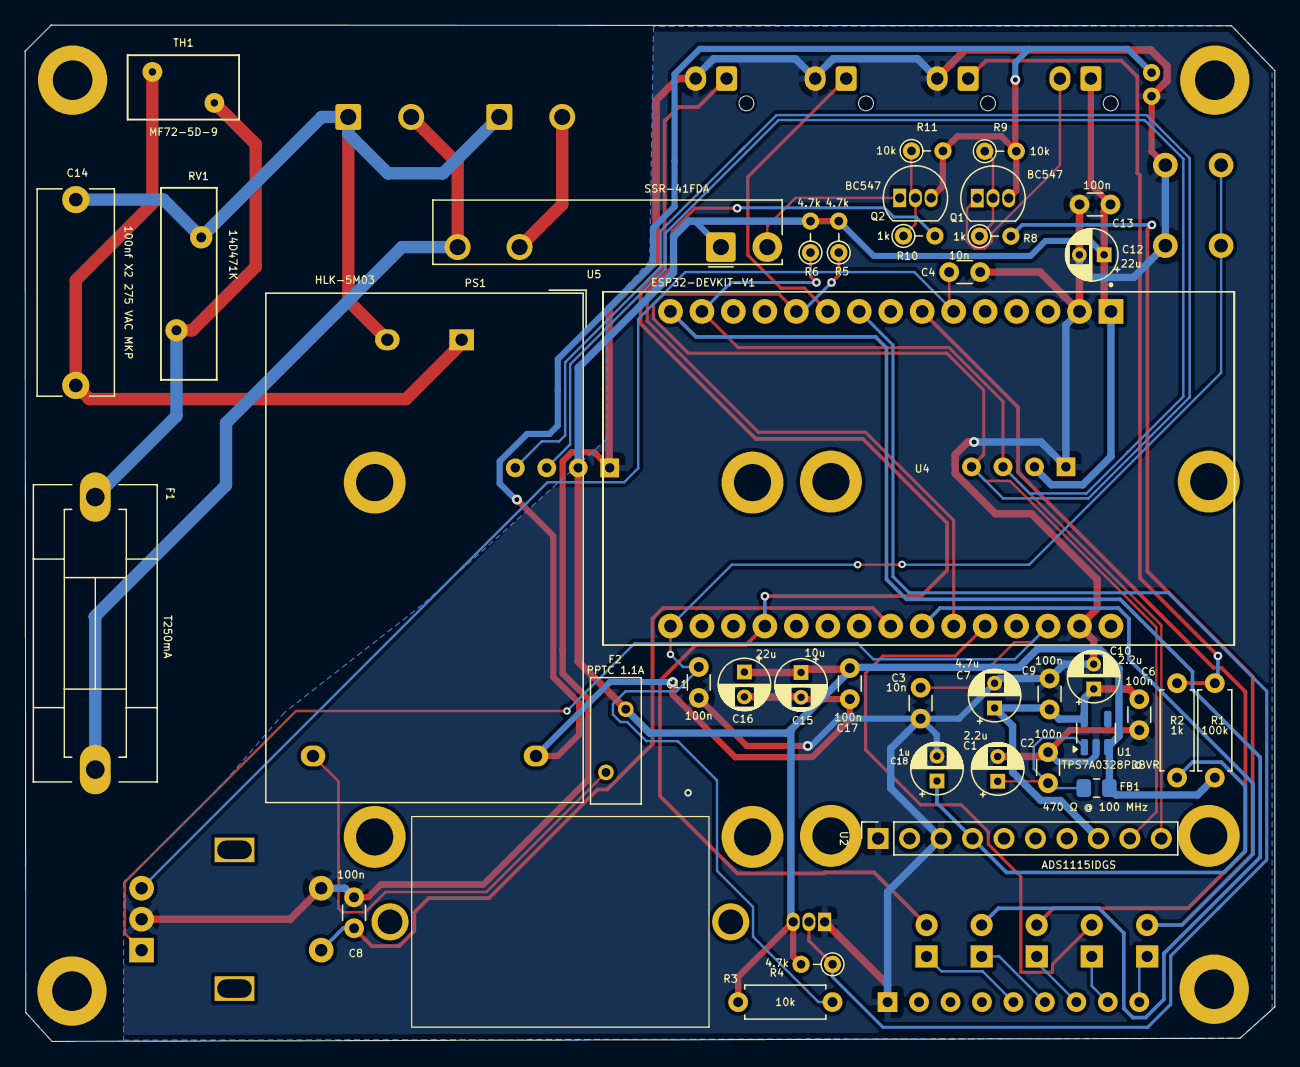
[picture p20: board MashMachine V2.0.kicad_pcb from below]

Board: 2 copper layers, 100.9 x 82.0 mm, 62 parts (40 on the bottom side), 36 nets.

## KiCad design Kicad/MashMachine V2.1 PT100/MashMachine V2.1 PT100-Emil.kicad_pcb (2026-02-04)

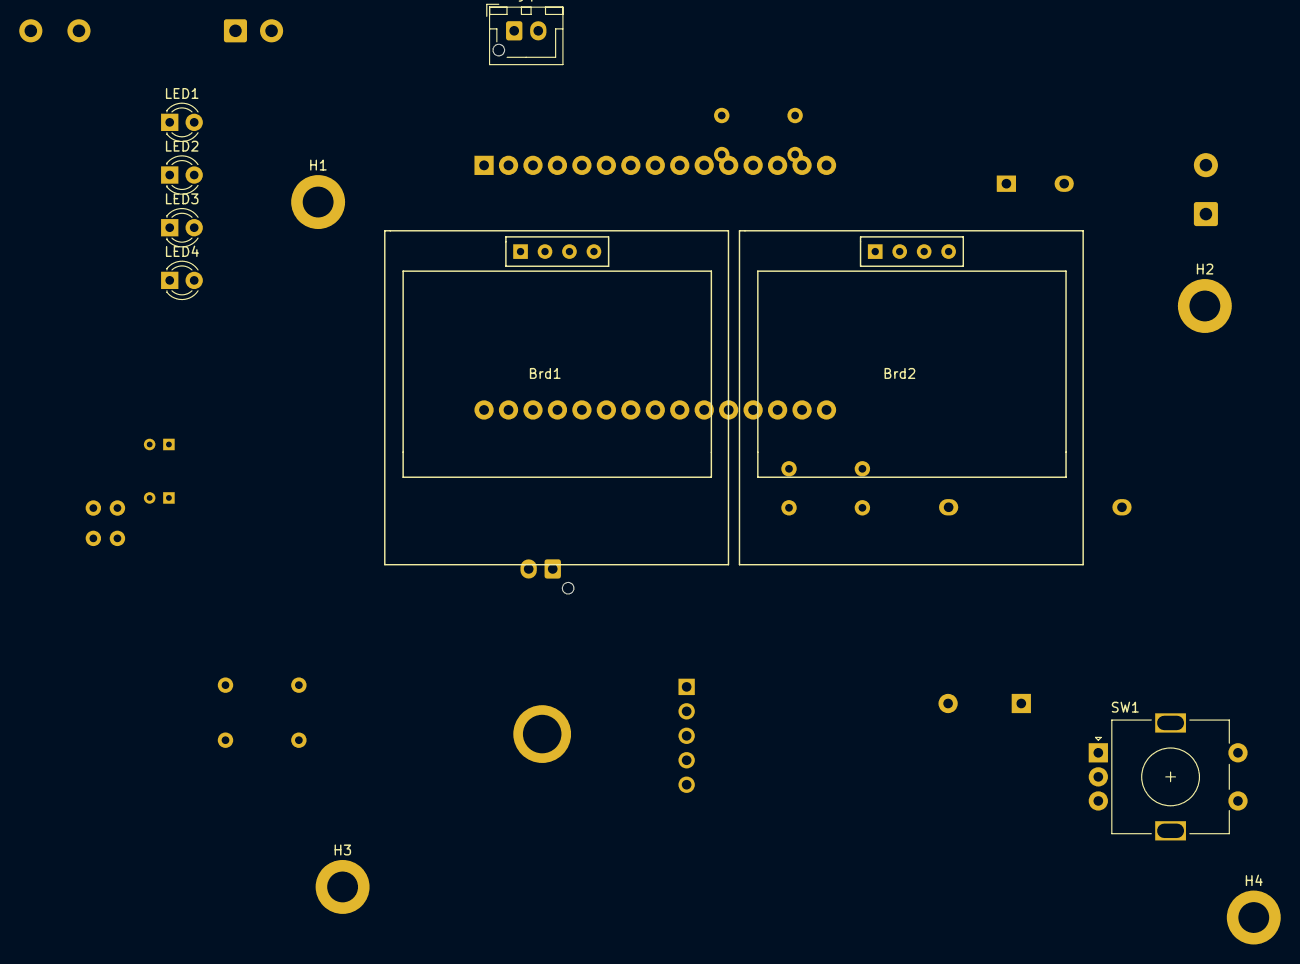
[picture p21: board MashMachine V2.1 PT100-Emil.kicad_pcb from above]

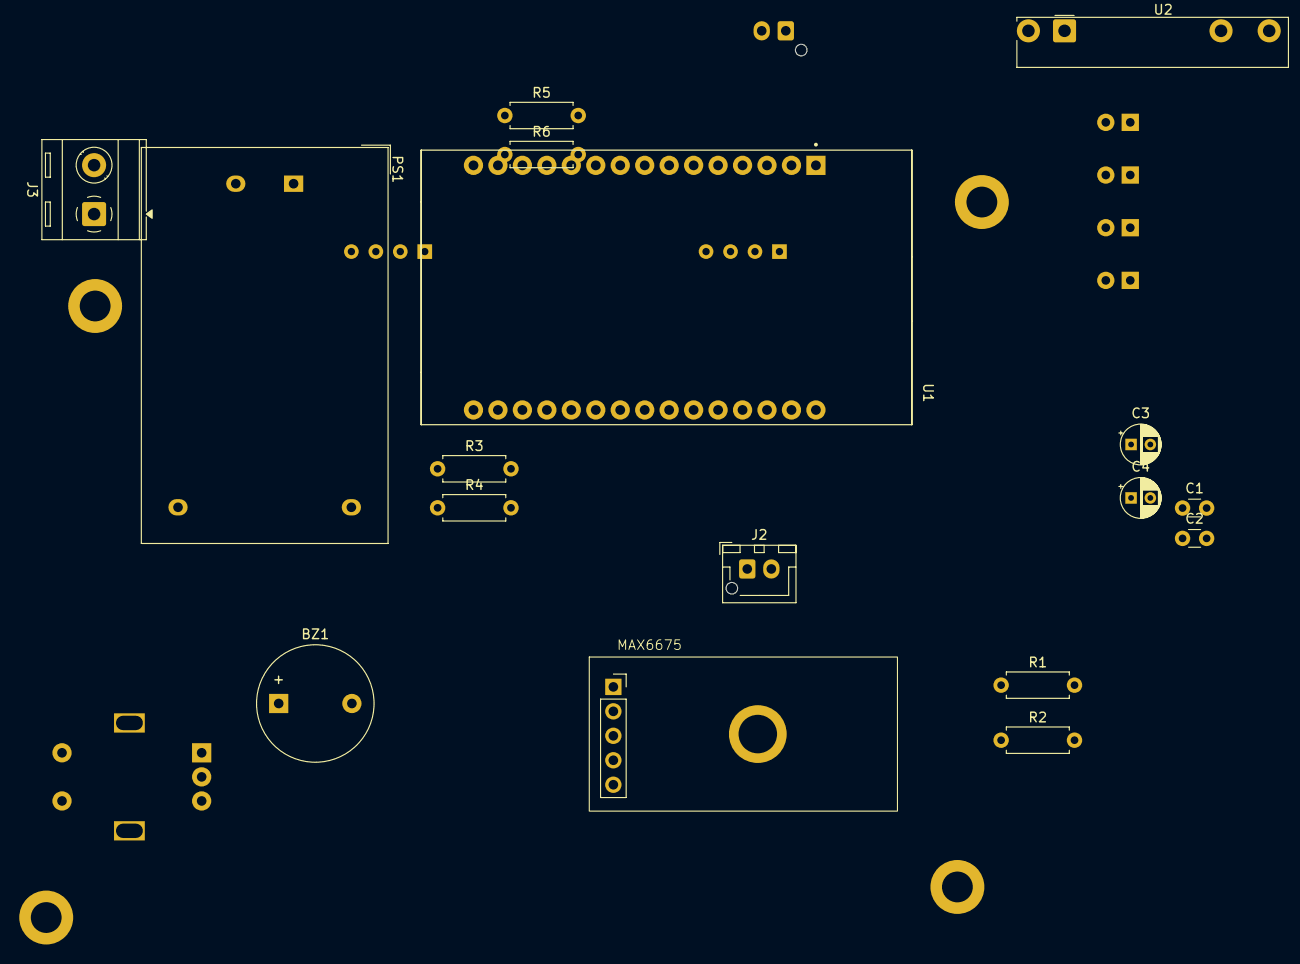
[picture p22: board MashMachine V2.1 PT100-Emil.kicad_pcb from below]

Board: 2 copper layers, 29 parts (17 on the bottom side), 21 nets, no tracks yet.

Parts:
BZ1: Alarm; Buzzer_12x9.5RM7.6
Brd1: SSD1306 Display 1, Addesss 0x78, (GND,VCC,SCL,SDA); ssd1306_1.3''
Brd2: SSD1306 Display 2, address 0x7A (GND,VCC,SCL,SDA); ssd1306_1.3''
C1, C2: 10n; C_Disc_D3.0mm_W1.6mm_P2.50mm
C3, C4: 100u; CP_Radial_D4.0mm_P2.00mm
H1, H2, H3, H4: MountingHole; MountingHole_3.2mm_M3_DIN965_Pad
J1: MAX6675
J2: Solid state Relay Out; JST_XH_B2B-XH-AM_1x02_P2.50mm_Vertical
J3: L1, N; TerminalBlock_RND_205-00287_1x02_P5.08mm_Horizontal
J4: pump; JST_XH_B2B-XH-AM_1x02_P2.50mm_Vertical
LED1: DC; LED_D3.0mm
LED2: On; LED_D3.0mm
LED3: Wifi reconnect; LED_D3.0mm
LED4: Mqtt_Reconnect; LED_D3.0mm
PS1: HLK-5M05; Converter_ACDC_Hi-Link_HLK-5Mxx
R1, R2, R3, R4: 1000; R_Axial_DIN0207_L6.3mm_D2.5mm_P7.62mm_Horizontal
R5, R6: 1k; R_Axial_DIN0207_L6.3mm_D2.5mm_P7.62mm_Horizontal
SW1: Rotary_Encoder_Switch; RotaryEncoder_Alps_EC11E-Switch_Vertical_H20mm
U1: ESP32-DEVKIT-V1; ESP32_DEVKIT_V1
U2: SSR-41FDA; Finder_34.81

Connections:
+3.3V: Brd1.2 (VCC), Brd2.2 (VCC), C4.1, J1.4, R5.2, R6.2
+5V: C3.1, PS1.4 (+Vout), U1.30 (VIN)
Alarm: BZ1.1 (-), U1.10 (D19)
GND: BZ1.2 (+), Brd1.1 (GND), Brd2.1 (GND), C1.2, C2.2, C3.2, C4.2, J1.5, J2.2, PS1.3 (-Vout), R1.1, R2.1, R3.1, R4.1, SW1.C, U1.2 (GND), U1.29 (GND), U2.A2
unnamed: J2.1, LED1.2 (A), U1.24 (D26)
unnamed: J3.1, PS1.1 (AC/L)
unnamed: J3.2, PS1.2 (AC/N)
unnamed: J4.1, U2.11
unnamed: J4.2, U2.14
unnamed: LED1.1 (K), R1.2
unnamed: LED2.2 (A), U1.26 (D14)
unnamed: LED2.1 (K), R2.2
unnamed: LED3.1 (K), R3.2
unnamed: LED4.1 (K), R4.2
unnamed: SW1.S1, U1.1 (3V3)
unnamed: C1.1, SW1.A, U1.28 (D13)
unnamed: SW1.S2, U1.23 (D25)
unnamed: C2.1, SW1.B, U1.6 (RX2)
PumpPin: U1.25 (D27), U2.A1
SCL: Brd1.3 (SCL), Brd2.3 (SCL), R6.1, U1.14 (D22)
SDA: Brd1.4 (SDA), Brd2.4 (SDA), R5.1, U1.11 (D21)

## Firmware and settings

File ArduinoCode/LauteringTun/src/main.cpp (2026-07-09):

#include "main.h"

//display1
uint8_t DISP_ITEM_ROWS; //4
uint8_t DISP_CHAR_WIDTH;
uint8_t CHAR_X;
uint8_t CHAR_Y;
//display2
uint8_t DISP2_ITEM_ROWS; //4
uint8_t DISP2_CHAR_WIDTH;
uint8_t DISP2_CHAR_X;
uint8_t DISP2_CHAR_Y;

//Homeassistant
//-----------------------------------------------------------------------
Privates privates; 
WiFiClient espClient; 
PubSubClient client(espClient); 
char messages[50]; 
volatile  bool TopicArrived = false;
const     int mqttpayloadSize = 16;
char mqttpayload [mqttpayloadSize] = {'\0'};
String mqtttopic;
//-----------------------------------------------------------------------
//rotary encoder
RotaryEncoderAccel encoder(outputA, outputB);  // GPIO32 och GPIO33 på ESP32
// ISR för båda pins, som anropas vid ändring (rising/falling)
void IRAM_ATTR handleInterrupt() {
  encoder.tick();
}
//-----------------------------------------------------------------------
// Buttons
PressButton btnOk(confirmBtnPin, 10); //debounce (ISR-attached inside library)
//-----------------------------------------------------------------------

enum pageType currPage = MENU_ROOT;

//-----------------------------------------------------------------------
//Menu internals
boolean updateAllItems = true;
boolean updateItemValue;
uint8_t itemCnt;
int8_t cursorPos;
uint8_t saveCursorPos;
uint8_t dispOffset;
uint8_t saveDispOffset;
bool edditing = false;
bool detectedRotation = false;
uint8_t root_pntrPos = 1;
uint8_t root_dispOffset = 0;
uint8_t flashCntr;
boolean flashIsOn;

Mysettings settings;
Mysettings oldSettings;
void sets_SetDeafault();
void sets_Load();
void sets_Save();
bool prevStartMashProgram_ = false;
bool prevStartHopProgram_ = false;
bool prevStartWhirlpoolProgram_ = false;
//-----------------------------------------------------------------------
//Time
unsigned long previousTime = 0; 
unsigned long currentTime;
double tS;
long passedTimeS_mashProgram = 0;
long passedTimeS_hopProgram = 0;
long passedTimeS_whirlpoolProgram = 0;
unsigned long previousSensorRead = 0;
const unsigned long saveInterval = 60000; // 60 000 ms = 60 sekunder
unsigned long lastEditTime = 0;
//-----------------------------------------------------------------------
//CONTROLLER
double Output_lauterTemp;
double current_lauterTemp;
double previous_lauterTemp;
double rawTemp;

double outdoorTemp; //received from home assistant (Norwegian Meteorological Institute)
double previous_outdoorTemp;
double indoorTemp; //received from home assistant (STM32f411 and esp32 xiao with bmp280 sensor)
double previous_indoorTemp;
double* ambientTempPtr = &outdoorTemp;

double DutyCycle = 0;
double previousDutyCycle = 0;
//                 y(t), u(t), r(t) 
// PID PID_lauterTemp(&current_lauterTemp, &Output_lauterTemp, &settings.targetTemp, &current_airTemp, settings.Kp_lauter, settings.Ki_lauter, 0, 0, DIRECT); //P_ON_M
PI_Controller lauterCtrl_PI(&current_lauterTemp, &Output_lauterTemp, &settings.targetTemp, ambientTempPtr); //PI controller with heat loss compensation
double lastKp = NAN;
double lastKHeat = NAN;
double lastDeadband1 = NAN;
double lastDeadband2 = NAN;
double lastGamma = NAN;
double currentHeaterPower_W = 0.0;
//-----------------------------------------------------------------------
// setting PWM properties
int freq = 5; //240
const int DC_Channel = 0;
const int resolution = 12;
//-----------------------------------------------------------------------
// Oled - Adafruit_SSD1306
U8G2_SH1106_128X64_NONAME_F_HW_I2C display1(U8G2_R0, /* reset=*/ U8X8_PIN_NONE);
U8G2_SH1106_128X64_NONAME_F_HW_I2C display2(U8G2_R0, /* reset=*/ U8X8_PIN_NONE);
u16_t timeLastTouched = 0;
bool displaySleeping = false;
//Oled - 2.42"
//-----------------------------------------------------------------------
double passedTime, previousPassedTime1, previousPassedTime2 = 0;
bool initPage = true;
bool changeValues [20];
//-----------------------------------------------------------------------
//MAX31865 PT100 - Mash temperature
  Adafruit_MAX31865 PT100(MAX31865_CS, MAX31865_SI, MAX31865_SO, MAX31865_SCK);
  double tempPT100 = 0;
  double filteredTempPT100 = 0;
  unsigned long lastReadTime = 0;
  const unsigned long readInterval = 1000;  // ms
  // ====== CONFIG ======
  #define RREF      435.8
  #define RNOMINAL  100.0
  // ---- Replace these with your measured values ----
  double const CAL_T1  = 8.7;     // Real temperature point 1 (ice bath)
  double const CAL_T2  = 99.5;   // Real temperature point 2 (boiling water)

  double const CAL_M1  = 9.3;     // Measured temperature at T1
  double const CAL_M2  = 98.2;   // Measured temperature at T2
  // ================================================
  // Calibration coefficients (computed automatically)
  double a;
  double b;

//-----------------------------------------------------------------------
//Water indicator
  bool waterDetected = true;
//-----------------------------------------------------------------------
// Loop time measurement variables
uint32_t last  = 0;
uint32_t now  = 0;
uint32_t loopTime  = 0;
uint32_t sumLoopTime = 0;
uint32_t loopCount = 0;
uint32_t avgLoopTime = 0;



void setup() {//=================================================SETUP=======================================================
  Serial.begin(115200);

  // WiFi.disconnect(true);
  // WiFi.mode(WIFI_OFF);

  PT100.begin(MAX31865_3WIRE);
   // Calculate calibration constants
  a = (CAL_T2 - CAL_T1) / (CAL_M2 - CAL_M1);
  b = CAL_T1 - a * CAL_M1;

  currentTime = millis();

  // configure LED PWM functionalitites
  ledcSetup(DC_Channel, freq, resolution);
  // attach the channel to the GPIO to be controlled
  ledcAttachPin(dutyCycleOutPin, DC_Channel);

  pinMode(ledOnPin, OUTPUT);
  pinMode(ledWaterDetectedPin, OUTPUT);
  pinMode(ledWifiPin, OUTPUT);
  // pinMode(ledMqttPin, OUTPUT);
  pinMode(confirmBtnPin, INPUT_PULLUP);
  pinMode(outputA, INPUT_PULLUP);
  pinMode(outputB, INPUT_PULLUP);
  //pinMode(NTC_PIN, INPUT);
  pinMode(pumpPin, OUTPUT);
  pinMode(alarmPin, OUTPUT);
  pinMode(waterDetectedPin, INPUT_PULLUP);

  // Initialize encoder interrupts (confirm button interrupt disabled)
  attachInterrupt(digitalPinToInterrupt(outputA), handleInterrupt, CHANGE);
  attachInterrupt(digitalPinToInterrupt(outputB), handleInterrupt, CHANGE);

  Wire.begin(21, 22);           // pins only

  // Serial.println("Scanning Wire...");
  // for (uint8_t addr = 1; addr < 127; addr++)
  // {
  //     Wire.beginTransmission(addr);
  //     uint8_t error = Wire.endTransmission();
  //     if (error == 0)
  //     {
  //         Serial.print("Found device at 0x");
  //         Serial.println(addr, HEX);
  //     }
  // }
  // Serial.println("Wire done");

  display1.setI2CAddress(0x3C << 1); 
  display1.begin();  
  display1.setBusClock(1000000);   
  display1.setFont(u8g2_font_6x12_mr);	// choose a suitable font
  display1.clearBuffer();					// clear the internal memory
  display1.setCursor(0, 0);

  DISP_CHAR_WIDTH = SCREEN_WIDTH / (display1.getMaxCharWidth()  + 0);          // hur många tecken per rad: display1.getMaxCharWidth();
  DISP_ITEM_ROWS =  SCREEN_HEIGHT / (display1.getMaxCharHeight()  + 3);         // max rader som får plats
  
  CHAR_X = display1.getMaxCharWidth() + 2; //margin
  CHAR_Y = display1.getMaxCharHeight() + 2; //margin

  display2.setI2CAddress(0x3D << 1);
  display2.begin();  
  display2.setBusClock(1000000); 
  display2.setFont(u8g2_font_6x12_mr);	// choose a suitable font  
  display2.clearBuffer();					// clear the internal memory
  display2.setCursor(0, 0);

  DISP2_CHAR_WIDTH = SCREEN_WIDTH / (display2.getMaxCharWidth()  + 2);          // hur många tecken per rad: display2.getMaxCharWidth();
  DISP2_ITEM_ROWS =  4;         // max rader som får plats
  
  DISP2_CHAR_X = display2.getMaxCharWidth() + 0; //margin
  DISP2_CHAR_Y = (SCREEN_HEIGHT / DISP2_ITEM_ROWS) + 0; //margin

  EEPROM.begin(sizeof(settings));
  sets_Load();

  //PT100 Temperature probe
  PT100.readRTD();
  rawTemp = PT100.temperature(RNOMINAL, RREF);

  // Apply two-point calibration
  
  double calibratedTemp = a * rawTemp + b;
  calibratedTemp = roundTo(calibratedTemp, 3); // Round to 3 decimal places
  tempPT100 = calibratedTemp;
  filteredTempPT100 = calibratedTemp;

  current_lauterTemp = tempPT100; //Temp_C;
  previous_lauterTemp = tempPT100; //Temp_C;

  updateAmbientSource(settings.brewingLocation);

  setupWiFi(); //Home assistant
  setupMQTT(); //Home assistant

  WiFi.onEvent([](WiFiEvent_t event) {
    if (event == ARDUINO_EVENT_WIFI_STA_DISCONNECTED) {
      if (client.connected()) {
        client.publish("esp32/wifi", "offline", true);
      }
    }
  });

  setupTime(); //NTP time for InfluxDB

  //(PI controller)
  lauterCtrl_PI.SetSampleTime(1000);   // ms
  // --- Output range ---
  lauterCtrl_PI.SetHeaterPowerLimits(0.0, heaterRatedPower_W);
  // --- Tunings ---
  lauterCtrl_PI.SetTunings(settings.Kp_lauter, 0, settings.k_heatLoss);
  // --- Safety / behavior ---
  lauterCtrl_PI.SetCaptureBands(settings.deadband1, settings.deadband2, settings.gamma); // °C  // Switch from full power to regulation at ±5 °C
  lauterCtrl_PI.SetIntegralLimit(0.25 * heaterRatedPower_W);
  // Start with feedforward only
  double Q0 = settings.k_heatLoss * (current_lauterTemp - *ambientTempPtr);
  lauterCtrl_PI.Reset(Q0);

}


void loop() { //=================================================LOOP=======================================================


  // loop time measurement
  // ---------------------------------------------------------
  now = micros();

  loopCount++;

  if (loopCount == 1)
      last = now;

  if (loopCount >= 100)
  {
      sumLoopTime = now - last;
      avgLoopTime = sumLoopTime / (loopCount - 1);

      if (avgLoopTime == 0) avgLoopTime = 1;

      loopCount = 0;
      last = now;
  }

  uint32_t freq = (avgLoopTime > 0) ? (1000000UL / avgLoopTime) : 0;

  // Serial.printf(
  //   "Loop:%4lu | LoopFreq:%6lu\n",
  //   avgLoopTime,
  //   freq
  // );
  // ---------------------------------------------------------

  passedTime = millis() * 0.001f; 

  float minutesSinceLastAction = (passedTime * 0.0166667f) - timeLastTouched;
  bool shouldSleep = (minutesSinceLastAction > settings.timeBeforeDisable);

  if (shouldSleep != displaySleeping)
  {
      displaySleeping = shouldSleep;
      display1.setPowerSave(displaySleeping);
      display2.setPowerSave(displaySleeping);
  }
    
  const float UPDATE_INTERVAL1 = 0.10;
  const float UPDATE_INTERVAL2 = 0.1;
  bool shouldUpdate1 = (passedTime - previousPassedTime1 >= UPDATE_INTERVAL1);
  bool shouldUpdate2 = (passedTime - previousPassedTime2 >= UPDATE_INTERVAL2);
  updateSettings();
  
  if(shouldUpdate1)
  {
    updateSensorValues(); 
    
    previousPassedTime1 = passedTime;

    float Q_W = 0.0;

    // =========================
    // MODE SUPERVISOR
    // =========================

    switch(settings.systemMode)
    {
      case MODE_CONTROL_Proportional:

        lauterCtrl_PI.Compute();
        Q_W = lauterCtrl_PI.GetCurrentPower_W();
        
          break;

      case MODE_MANUAL:
          Q_W = settings.manualPower;
          break;
    }

    // Saturate power
    Q_W = constrain(Q_W, 0.0, heaterRatedPower_W);

    // Convert to PWM
    float rawDuty = Q_W * W_to_PWM;

    if(settings.power && waterDetected) 
    {
      previousDutyCycle = DutyCycle;
      DutyCycle = Filter(rawDuty , previousDutyCycle, settings.filterDC, 4095.0); 
    }
    else 
    {
      DutyCycle = 0;
    }
    // --- Apply output ---
    ledcWrite(DC_Channel, DutyCycle);
    // Serial.print(", DutyCycle: ");
    // Serial.print(DutyCycle);
  }
  

  if (updateAllItems)
    display1.clearBuffer();

  switch (currPage)
  {
    case MENU_ROOT: page_MenuRoot(); break;
    case MENU_MODE: page_MENU_MODE(); break;
    case MENU_CONTROL_MODE_Proportional: page_MENU_CONTROL_MODE_Proportional(); break;
    case MENU_MANUAL_MODE: page_MENU_MANUAL_MODE(); break;
    case MENU_MISC: page_MENU_MISC(); break;
    case MENU_BREWING_LOCATION: page_MENU_BREWING_LOCATION(); break;
  }
  if (updateAllItems || updateItemValue)
  {
    display1.sendBuffer();                        //välldigt långsam
    updateAllItems = false;
    updateItemValue = false;
  }

  // printPointer();     // this one take long time
  if (current_lauterTemp != previous_lauterTemp || outdoorTemp != previous_outdoorTemp || indoorTemp != previous_indoorTemp || DutyCycle != previousDutyCycle || settings.targetTemp != oldSettings.targetTemp)
  {
    updateDisp2();
    previousPassedTime2 = passedTime;
  } 
  
  //Homeassistant
  if(passedTime - previousTime >= 1.0) {publishMessage(); previousTime = passedTime;}

  detectedRotation = encoder.getDirection() != RotaryEncoderAccel::Direction::NOROTATION;
  if(detectedRotation)
  {
    lastEditTime = millis();
  }
  // Consume confirm button timestamp from library ISR and update touch timers
  {
    uint32_t t = btnOk.consumeTouchMs();
    if (t != 0) {
      timeLastTouched = t/1000.0/60.0;
      lastEditTime = t;
    }
  }

  // === WiFi reconnect ===
  if (WiFi.status() != WL_CONNECTED) {
    reconnectWiFi();
  }

  // === MQTT reconnect ===
   if (!client.connected()) {
    reconnectMQTT();
  }

  // === MQTT keep-alive ===
  client.loop();


}

void page_MenuRoot(){//=================================================ROOT_MENU============================================
  if(initPage)
  {
    cursorPos = root_pntrPos;
    dispOffset = root_dispOffset;

    initMenuPage(F("MAIN MENU"), 2);
    initPage = false;
  }

  if(btnOk.Pressed())
  {
    FlashPointer();
    root_pntrPos = cursorPos;
    root_dispOffset = dispOffset;
    initPage = true;
    switch (cursorPos)
    {
      case 0: currPage = MENU_MODE;         changeValues[0] = false; edditing = false; return;
      case 1: currPage = MENU_MISC;         changeValues[1] = false; edditing = false; return;
    }
  }
  else
    doPointerNavigation();

  if(!(updateAllItems || updateItemValue)) return;

  for(uint8_t i = 1; i <= 2; i++)
  {
    if(menuItemPrintable(1, i))
    {
      switch(i)
      {
        case 1: display1.print(F("MODE ->            ")); break;
        case 2: display1.print(F("MISC               ")); break;
      }
    }

    if(menuItemPrintable(7, i))
    {
      switch(i)
      {
        case 1: printStringAtWidth(systemModeToString(settings.systemMode), 4); break;
      }
    }
  }
}

void page_MENU_MODE(){//=================================================MODE============================================
  if(initPage)
  {
    cursorPos = 0;
    dispOffset = 0;
    initMenuPage(F("MODE"), 4);
    initPage = false;
  }

  if(btnOk.Pressed())
  {
    switch (cursorPos)
    {
      case 0: FlashPointer(); initPage = true; currPage = MENU_CONTROL_MODE_Proportional; return;
      case 1: FlashPointer(); initPage = true; currPage = MENU_MANUAL_MODE; return;
      case 3: FlashPointer(); initPage = true; currPage = MENU_ROOT; sets_Save(); return;
      default: return;
    }
  }
  else
    doPointerNavigation();


  if(!(updateAllItems || updateItemValue)) return;

  for(uint8_t i = 1; i <= 4; i++)
  {
    if(menuItemPrintable(1, i))
    {
      switch(i)
      {
        case 1: display1.print(F("CONTROL MODE (Kp) ")); break;
        case 2: display1.print(F("MANUAL MODE       ")); break;
        case 3: display1.drawHLine(5, display1.getCursorY(), 120); break;
        case 4: display1.print(F("Back              ")); break;
      }
    }
  }
}

void page_MENU_CONTROL_MODE_Proportional(){
  //=================================================CONTROL_MODE_Proportional============================================
  if(initPage)
  {
    cursorPos = 0;
    dispOffset = 0;
    initMenuPage(F("CONTROL MODE (Kp)"), 9);
    memset(changeValues, 0, sizeof(changeValues));
    initPage = false;
  }

  if(btnOk.Pressed())
  {
    FlashPointer();
    changeValues[cursorPos] = !changeValues[cursorPos];
    edditing = !edditing;
  }

       if(changeValues[0]){*&settings.systemMode = MODE_CONTROL_Proportional; changeValues [0] = false; updateItemValue = true; }
  else if(changeValues[1]){incrementDecrementDouble(&settings.targetTemp, 1.0, 5.0, settings.maxMashTemp); settings.targetTemp = round(settings.targetTemp);}
  else if(changeValues[2])incrementDecrementDouble(&settings.Kp_lauter, 0.1, 0.0, 50.0);
  else if(changeValues[3])incrementDecrementDouble(&settings.k_heatLoss, 0.025, 0.0, 5.0);
  else if(changeValues[4])incrementDecrementDouble(&settings.deadband1, 0.5, settings.deadband2, 20.0);
  else if(changeValues[5])incrementDecrementDouble(&settings.deadband2, 0.1, 0.0, settings.deadband1);
  else if(changeValues[6])incrementDecrementDouble(&settings.gamma, 0.01, 0.0, 1.0);
  else if(changeValues[8]) {currPage = MENU_ROOT; sets_Save(); changeValues[7] = false; initPage = true;}
  else 
    doPointerNavigation(); 

  if(!(updateAllItems || updateItemValue)) return;

  display1.drawVLine(9 * CHAR_X, 0, 64);

  for(uint8_t i = 1; i <= 9; i++)
  {
    if(menuItemPrintable(1, i))
    {
      switch(i)
      {
        case 1: display1.print(F("Activate ")); break;
        case 2: display1.print(F("Setpoint ")); break;
        case 3: display1.print(F("Kp       ")); break;
        case 4: display1.print(F("k_heat   ")); break;
        case 5: display1.print(F("Band 1   ")); break;
        case 6: display1.print(F("Band 2   ")); break;
        case 7: display1.print(F("Gamma    ")); break;
        case 8: display1.drawHLine(5, display1.getCursorY(), 120); break;
        case 9: display1.print(F("Back     ")); break;
      }
    }
    if(menuItemPrintable(10, i))
    {
      switch(i)
      {
        case 1: printOnOff(settings.systemMode == MODE_CONTROL_Proportional); break;
        case 2: printInt32_tAtWidth((uint32_t)settings.targetTemp, 3, "C"); break;
        case 3: printDoubleAtWidth(settings.Kp_lauter, 4, "W/C"); break;
        case 4: printDoubleAtWidth(settings.k_heatLoss, 4, "W/C", 2); break;
        case 5: printDoubleAtWidth(settings.deadband1, 4, "C"); break;
        case 6: printDoubleAtWidth(settings.deadband2, 3, "C"); break;
        case 7: printDoubleAtWidth(settings.gamma, 4, " ", 2); break;
      }
    }
  }
}

void page_MENU_MANUAL_MODE(){//=================================================MANUAL_MODE============================================

  if(initPage)
  {
    cursorPos = 0;
    dispOffset = 0;
    initMenuPage(F("MANUAL MODE"), 3);
    memset(changeValues, 0, sizeof(changeValues));
    initPage = false;
  }
  
  if(btnOk.Pressed())
  {
    FlashPointer();

    switch (cursorPos)
    {
      case 0: changeValues[0] = !changeValues[0]; edditing = !edditing; break;
      case 1: changeValues[1] = !changeValues[1]; edditing = !edditing; break;
      case 2: currPage = MENU_MODE; sets_Save(); initPage = true; return;
    }
  }

       if(changeValues[0]){*&settings.systemMode = MODE_MANUAL; changeValues [0] = false; updateItemValue = true; }
  else if(changeValues[1]) incrementDecrementDouble(&settings.manualPower, 1.0, 0.0, heaterRatedPower_W);
  else 
    doPointerNavigation();

  if(menuItemPrintable(1,1)){display1.print(F("Activate               "));}
  if(menuItemPrintable(1,2)){display1.print(F("Power                  "));}
  if(menuItemPrintable(1,3)){display1.print(F("Back                   "));}

  if(menuItemPrintable(10,1)){printOnOff(settings.systemMode == MODE_MANUAL);}
  if(menuItemPrintable(10,2)){printDoubleAtWidth(settings.manualPower, 4, "W", 1);}

}
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

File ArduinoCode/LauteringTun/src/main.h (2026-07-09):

#pragma once
#include <Arduino.h>
#include <mash_config.h>
#include <Wire.h>
#include <U8g2lib.h>
#include <PI_Controller.h>
#include <PressButton.h>
#include <RotaryEncoderAccel.h>
#include <EEPROM.h>
#include <WiFi.h>
#include <PubSubClient.h>
#include <Privates.h>
#include <ArduinoJson.h>
#include <math.h>
#include <Adafruit_MAX31865.h>
#include <OneWire.h>
#include <HTTPClient.h>
#include <time.h>

// -----------------------------------------------------------------------
// IO-pins
#define dutyCycleOutPin     26
#define ledOnPin            14
#define ledWaterDetectedPin  4
#define ledWifiPin          17
#define outputA             33
#define outputB             32
#define confirmBtnPin       25
#define MAX31865_CS          5
#define MAX31865_SO         19
#define MAX31865_SCK        18
#define MAX31865_SI         23
#define pumpPin             27
#define alarmPin            13
#define waterDetectedPin    34

// -----------------------------------------------------------------------
// OLED display
#define SCREEN_WIDTH  128
#define SCREEN_HEIGHT  64

// -----------------------------------------------------------------------
// Settings constants
#define PACING_MC       30
#define FLASH_RST_CNT    3
#define SETTINGS_CHKVAL  3647
#define SHIFT_UP         0

// PT100 calibration
#define RREF      435.8
#define RNOMINAL  100.0

// -----------------------------------------------------------------------
// Enums

enum BrewingLocation {
    OutDoor,
    InDoor
};

//Menu pages
enum pageType {
    MENU_ROOT,
    MENU_MODE,
    MENU_CONTROL_MODE_Proportional,
    MENU_MANUAL_MODE,
    MENU_MISC,
    MENU_BREWING_LOCATION
};

//System Mode
enum SystemMode {
  MODE_CONTROL_Proportional,
  MODE_MANUAL
};

// -----------------------------------------------------------------------
// Settings struct
#pragma pack(1)
struct Mysettings {
    double  Kp_lauter         = 12.0;
    double  k_heatLoss        = 0.4;
    double  deadband1         = 8;
    double  deadband2         = 1;
    double  gamma             = 0.35;
    double  targetTemp        = 25;
    SystemMode systemMode = MODE_CONTROL_Proportional;
    double manualPower = 0;
    BrewingLocation brewingLocation = OutDoor;
    int16_t timeBeforeDisable = 4;
    boolean power             = true;
    int16_t maxMashTemp       = 100;
    double  filter_adc1       = 0.0f;
    double  filterDC          = 0.3f;
    int16_t alarmVolume       = 4;
    int16_t alarmTime         = 3;
    uint16_t settingsCheckValue = SETTINGS_CHKVAL;
};

// -----------------------------------------------------------------------
// Global variable declarations (defined in main.cpp)

// Display sizing
extern uint8_t DISP_ITEM_ROWS;
extern uint8_t DISP_CHAR_WIDTH;
extern uint8_t CHAR_X;
extern uint8_t CHAR_Y;
extern uint8_t DISP2_ITEM_ROWS;
extern uint8_t DISP2_CHAR_WIDTH;
extern uint8_t DISP2_CHAR_X;
extern uint8_t DISP2_CHAR_Y;

// Settings
extern Mysettings settings;
extern Mysettings oldSettings;

// MQTT / WiFi
extern Privates      privates;
extern WiFiClient    espClient;
extern PubSubClient  client;
extern char          messages[50];
extern volatile bool TopicArrived;
extern char          mqttpayload[];
extern String        mqtttopic;

// Encoder / button
extern RotaryEncoderAccel encoder;
extern PressButton        btnOk;

// Menu state
extern pageType  currPage;
extern boolean   updateAllItems;
extern boolean   updateItemValue;
extern uint8_t   itemCnt;
extern int8_t    cursorPos;
extern uint8_t   saveCursorPos;
extern uint8_t   dispOffset;
extern uint8_t   saveDispOffset;
extern bool      edditing;
extern bool      detectedRotation;
extern uint8_t   root_pntrPos;
extern uint8_t   root_dispOffset;
extern uint8_t   flashCntr;
extern boolean   flashIsOn;
extern bool      changeValues[20];
extern bool      initPage;

// Timing
extern unsigned long previousTime;
extern unsigned long currentTime;
extern double        tS;
extern unsigned long previousSensorRead;
extern unsigned long lastEditTime;
extern double        passedTime;
extern double        previousPassedTime1;
extern double        previousPassedTime2;

// Controller / temperatures
extern double Output_lauterTemp;
extern double current_lauterTemp;
extern double previous_lauterTemp;
extern double rawTemp;
extern double outdoorTemp;
extern double indoorTemp;
extern double previous_indoorTemp;
extern double previous_outdoorTemp;
extern double* ambientTempPtr;
extern double DutyCycle;
extern double previousDutyCycle;
extern double lastKp, lastKi, lastKHeat, lastDeadband1, lastDeadband2, lastGamma;
extern double currentHeaterPower_W;

extern PI_Controller lauterCtrl_PI;

// PWM
extern int       freq;
extern const int DC_Channel;
extern const int resolution;

// OLED
extern U8G2_SH1106_128X64_NONAME_F_HW_I2C display1;
extern U8G2_SH1106_128X64_NONAME_F_HW_I2C display2;
extern u16_t timeLastTouched;
extern bool  displaySleeping;
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

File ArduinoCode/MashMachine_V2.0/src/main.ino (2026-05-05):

#include <Arduino.h>
#include <mash_config.h> //config.h
#include <Wire.h> //temperatur
// #include <Adafruit_GFX.h> //oled
// #include <Adafruit_SSD1306.h> //oled
#include <U8g2lib.h> //oled
// #include <Adafruit_I2CDevice.h>
#include <PI_Controller.h> //PI controller with heat loss compensation
#include "Controllers/LQG_Controller.h"
#include "Controllers/Boil_Controller.h"
#include "Linear_SSM_Models/Model_50C.h"
#include "Linear_SSM_Models/Model_65C.h"
#include "Linear_SSM_Models/Model_75C.h"
#include "Linear_SSM_Models/Model_Boil.h"
#include "Excitation.h" //identification signal generator
#include <PressButton.h> //Interface
#include <RotaryEncoderAccel.h> //Interface
#include <EEPROM.h> //Save Settings
#include <WiFi.h> //Home assistant
#include <PubSubClient.h> //Home assistant
#include <Privates.h> //Homeassistant 
#include <ArduinoJson.h> //Homeassistant
#include <math.h> //math
#include <Adafruit_MAX31865.h> //temperatur
#include <OneWire.h> //temperatur
#include <DallasTemperature.h> //temperatur
#include <HTTPClient.h>      //InfluxDB
#include <time.h> //time for InfluxDB


//-----------------------------------------------------------------------
//Model och enums
enum ModelID { MODEL_50, MODEL_65, MODEL_75, MODEL_Boil };
//-----------------------------------------------------------------------

// Hop icon, 48x48px
static const unsigned char hop_logo[] PROGMEM = {
  0x00, 0x00, 0x00, 0xC0, 0xCC, 0x00, 0x00, 0x00, 0x00, 0x70, 0xEF, 0x01, 0x00, 0x00, 0x20, 0x78,
  0x07, 0x00, 0x00, 0x00, 0x20, 0x38, 0x60, 0x0C, 0x00, 0x00, 0x20, 0x38, 0xE0, 0x0D, 0x00, 0x00,
  0x20, 0x82, 0xDF, 0x05, 0x00, 0x00, 0x00, 0x03, 0xBF, 0x01, 0x00, 0x00, 0x00, 0xFB, 0xBC, 0x04,
  0x00, 0x00, 0x00, 0xFF, 0xDD, 0x06, 0x00, 0x38, 0x00, 0xFF, 0x1D, 0x02, 0x00, 0xF8, 0x00, 0xFE,
  0x0D, 0x01, 0x00, 0xE0, 0x01, 0xFE, 0x26, 0x00, 0xC0, 0xE7, 0x01, 0xFC, 0xF0, 0x00, 0xE0, 0xF3,
  0x03, 0x7C, 0x78, 0x00, 0xF0, 0xF3, 0x07, 0x1C, 0x01, 0x00, 0xF0, 0xFB, 0x01, 0x9C, 0x1F, 0x00,
  0x08, 0x78, 0x00, 0xD8, 0x1F, 0x00, 0x60, 0x38, 0xFF, 0x17, 0x07, 0x00, 0x30, 0x9D, 0xFF, 0x0F,
  0x98, 0x00, 0x38, 0xDD, 0xFF, 0x0F, 0xCC, 0x03, 0xBC, 0x4D, 0xFE, 0x19, 0xCC, 0x07, 0x9E, 0x0D,
  0xFE, 0x01, 0x1E, 0x00, 0xC2, 0x4B, 0xFE, 0x09, 0x3E, 0x0C, 0xC0, 0xE3, 0xFE, 0x19, 0x7F, 0x1C,
  0xD6, 0xE7, 0xFC, 0x3D, 0x7F, 0x19, 0xD2, 0xF7, 0xFC, 0x3C, 0x7F, 0x03, 0xD3, 0xF7, 0xFC, 0xFC,
  0x79, 0x47, 0x9B, 0x73, 0xF8, 0x78, 0x81, 0x57, 0x39, 0x38, 0x7A, 0x71, 0xEE, 0x97, 0xF8, 0x19,
  0x36, 0x61, 0x0E, 0x33, 0xFA, 0x50, 0x8E, 0x69, 0x0C, 0x7C, 0x02, 0xD0, 0xFE, 0x49, 0xEC, 0xC0,
  0x06, 0xC3, 0xFC, 0x1D, 0xD8, 0xC0, 0xCE, 0xC1, 0xFC, 0x1C, 0x80, 0x1D, 0xE6, 0xE0, 0xF8, 0x1C,
  0x00, 0x00, 0x00, 0xE0, 0x78, 0x18, 0x00, 0x00, 0x00, 0x40, 0x70, 0x18, 0x00, 0x00, 0x00, 0x40,
  0xA4, 0x18, 0x00, 0x00, 0x00, 0x00, 0xCC, 0x00, 0x00, 0x00, 0x00, 0x00, 0xFD, 0x04, 0x00, 0x00,
  0x00, 0x00, 0xF9, 0x06, 0x00, 0x00, 0x00, 0x00, 0x7B, 0x06, 0x00, 0x00, 0x00, 0x00, 0x33, 0x03,
  0x00, 0x00, 0x00, 0x00, 0x0B, 0x03, 0x00, 0x00, 0x00, 0x00, 0x5A, 0x01, 0x00, 0x00, 0x00, 0x00,
  0x78, 0x00, 0x00, 0x00, 0x00, 0x00, 0x30, 0x00, 0x00, 0x00, 0x00, 0x00, 0x20, 0x00, 0x00, 0x00,
};

//IO-pins
#define dutyCycleOutPin 26 //    green LED
#define ledOnPin 14 //           orange LED
#define ledWaterDetectedPin 4 // red LED
#define ledWifiPin 17 //         blue LED
//#define ledMqttPin 23 //         yellow LED
//rotary encoder
#define outputA 32//32
#define outputB 33//33
#define confirmBtnPin 25 // pin 25 ESP32 - ok
// // MAX31865 PT100
#define MAX31865_CS 5 //MAX31865 chip select
#define MAX31865_SO 19 //MAX31865 serial out
#define MAX31865_SCK 18 //MAX31865 serial clock
#define MAX31865_SI 23 //MAX31865 serial in
//Pump
#define pumpPin 27 //ESP32 - Pump
//Larm
#define alarmPin 13//13 // ESP32 - alarm
//
#define ONE_WIRE_BUS 16// 16 //ESP32 - OneWire bus
//Water indicator
//#define waterDetectedPin adc2 ads1115
#define waterDetectedPin 34
//-----------------------------------------------------------------------
// OLED display
#define SCREEN_WIDTH 128 // OLED display width, in pixels
#define SCREEN_HEIGHT 64 // OLED display height, in pixels
//-----------------------------------------------------------------------
//Settings
#define PACING_MC 30 //25
#define FLASH_RST_CNT 3 //30
#define SETTINGS_CHKVAL 3647 
#define SHIFT_UP 0 //240/8
//display1
uint8_t DISP_ITEM_ROWS; //4
uint8_t DISP_CHAR_WIDTH;
uint8_t CHAR_X;
uint8_t CHAR_Y;
//display2
uint8_t DISP2_ITEM_ROWS; //4
uint8_t DISP2_CHAR_WIDTH;
uint8_t DISP2_CHAR_X;
uint8_t DISP2_CHAR_Y;

//-----------------------------------------------------------------------
//Varibles

//Homeassistant
//-----------------------------------------------------------------------
Privates privates; 
WiFiClient espClient; 
PubSubClient client(espClient); 
char messages[50]; 
volatile  bool TopicArrived = false;
const     int mqttpayloadSize = 16;
char mqttpayload [mqttpayloadSize] = {'\0'};
String mqtttopic;
//-----------------------------------------------------------------------
//rotary encoder
RotaryEncoderAccel encoder(outputA, outputB);  // GPIO32 och GPIO33 på ESP32
// ISR för båda pins, som anropas vid ändring (rising/falling)
void IRAM_ATTR handleInterrupt() {
  encoder.tick();
}
//-----------------------------------------------------------------------
// Buttons
PressButton btnOk(confirmBtnPin, 10); //debounce (ISR-attached inside library)
//-----------------------------------------------------------------------
//System Mode
enum SystemMode {
  MODE_CONTROL_LQG,
  MODE_CONTROL_PI,
  MODE_IDENTIFICATION,
  MODE_MANUAL
};
//Identification type
enum IdentificationType {
  IDENT_SINE,
  IDENT_MULTI_SINE,
  IDENT_STEP_RESPONSE
};

const char* identificationTypeToString(IdentificationType type);
const char* systemModeToString(SystemMode mode);

Excitation excitation;

enum BrewingLocation {
  OutDoor,
  InDoor
};

const char* brewingLocationToString(BrewingLocation location);
void updateAmbientSource(BrewingLocation loc);

//Menu structure
enum pageType{
  MENU_ROOT,
  MENU_MODE,
  MENU_CONTROL_MODE_LQG,
  MENU_CONTROL_MODE_PI,
  MENU_IDENT_MODE,
  MENU_IDENT_TYPE,
  MENU_IDENT_SINE,
  MENU_IDENT_MULTI_SINE,
  MENU_IDENT_STEP_RESPONSE,
  MENU_MANUAL_MODE,
  MENU_MISC,
  MENU_BREWING_LOCATION,
  MENU_MASH_PROGRAM,
  MENU_HOPS_PROGRAM,
  MENU_WHIRLPOOL_PROGRAM
};
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

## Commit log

2025-04-03 added main with loadCompensation
    [Mash Tank Bottom.stl, Mash Tank Box.0003.iam, Mash Tank Box.0014.ipt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]
2025-08-16 added comments
    [8_button_macro_keypad_-_top_plate.ipt, MashMachine.kicad_sch]
2025-08-25 added rotoryEncoderAccel library, modified main_with_load_comp.ino
2025-08-28 modified main, rotaryEncoderAccel and kicad
2025-08-28 removed kicad backups
2025-12-19 added new libraries and json format for publish message
    [MashMachine-B.Cu.gbl, MashMachine-B.Mask.gbs, MashMachine-B.Paste.gbp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]
2026-02-04 added kicad mashMachine V2.0
    [MashMachine V2-B_Cu.gbl, MashMachine V2-B_Mask.gbs, MashMachine V2-B_Paste.gbp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]
2026-04-02 added loop timer, added exition.cpp and exitation.h, modified rotaryEncoderAccel, modified LQG_Controller.cpp
2026-05-05 changed a lot of stuff
    [BeerMakingShelf.0038.iam, BeerMakingShelf.iam, FermentingTun.0002.ipt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]
2026-05-27 new SSM models, main.ino deleted, main.cpp created, New Makefile, etc
    [Assembly-quarl-LinuxOS-safeBackup-0001.iam, Assembly.iam, CE3V3SE_lid_lautering_tank.3mf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]
